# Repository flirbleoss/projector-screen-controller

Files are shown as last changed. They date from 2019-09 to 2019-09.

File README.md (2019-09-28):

# Projector Screen Controller

Simple controller for basic motorized projector screens. An _almost_-drop-in
replacement for the Da-Lite SCB-100.

Status: _Work in progress_

# Background

Tired of the commercial screen controller letting out its magic smoke every
couple of years and not content with the $400 replacement cost, I decided to
make my own _almost_-drop-in replacement with more emphasis on electronic
protection than the commercial variant seems to have.

In my analysis of both SCB-100s that failed, it appeared a transient condition
upset the MAX232 driver such that it causes a dead-short between the 5v and 0v
rails. The charge pump capacitors of the MAX232 chip are adjacent to the
ULN2003 relay driver and the 12V decoupling capacitor. The design relies on
the diodes in the ULN2003 for back-EMF suppression, which I speculate may not
be adequate for the off-brand relays in use in both of my SCB-100s (an online
search reveals other specimens have relays from a more reputable brand,
however.) Finally, the switching power supply module is soldered to the back
of the logic board. While there is a plastic divider between the boards, there
is only a few milimeters of space and line voltage spikes may well cause
interference; additionally there are several places where line voltage and
signal voltage traces come closer than I would be comfortable with.

It is my conclusion therefore that the failures are likely caused by
insufficient physical isolation and insufficient transient back-EMF
suppression.

## Design objectives

* Same form-factor for the board, so it can use the same metal case
  in-situ.
* Connections in roughly the same locations, with the same pin ordering.
* Use removable Phoenix connectors with screw terminals throughout.
* Improved electronic protection;
  * Better flyback suppression from the relays.
  * DC power protection in case the power supply fails.
  * Physical board isolation (with board cut-outs) between line voltages
    and the 5V/12V sections, especially around the relays.
  * Better isolation between 12V and 5V sections, to avoid relay noise
    issues.
  * Modern high-efficiency switching power supply with plenty of
    protection features.
* More indicator LEDs to show what is going on.
* Backward-compatible RS232 protocol, but enhancements to allow
  customizing, for example, the motor run time.
* Open-source design.

# Implementation

## Preview

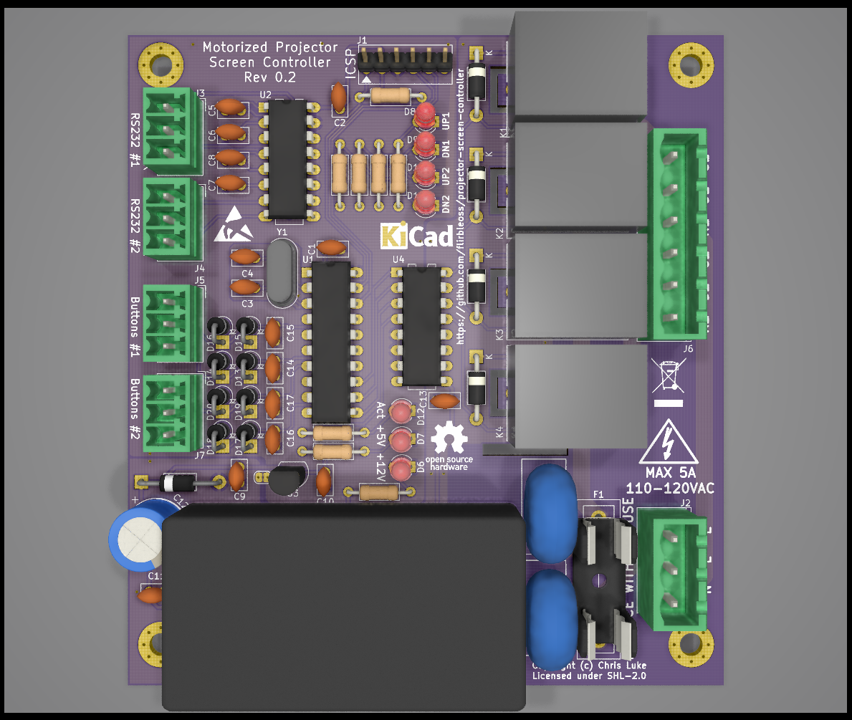
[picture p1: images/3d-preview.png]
3D board preview (with components)

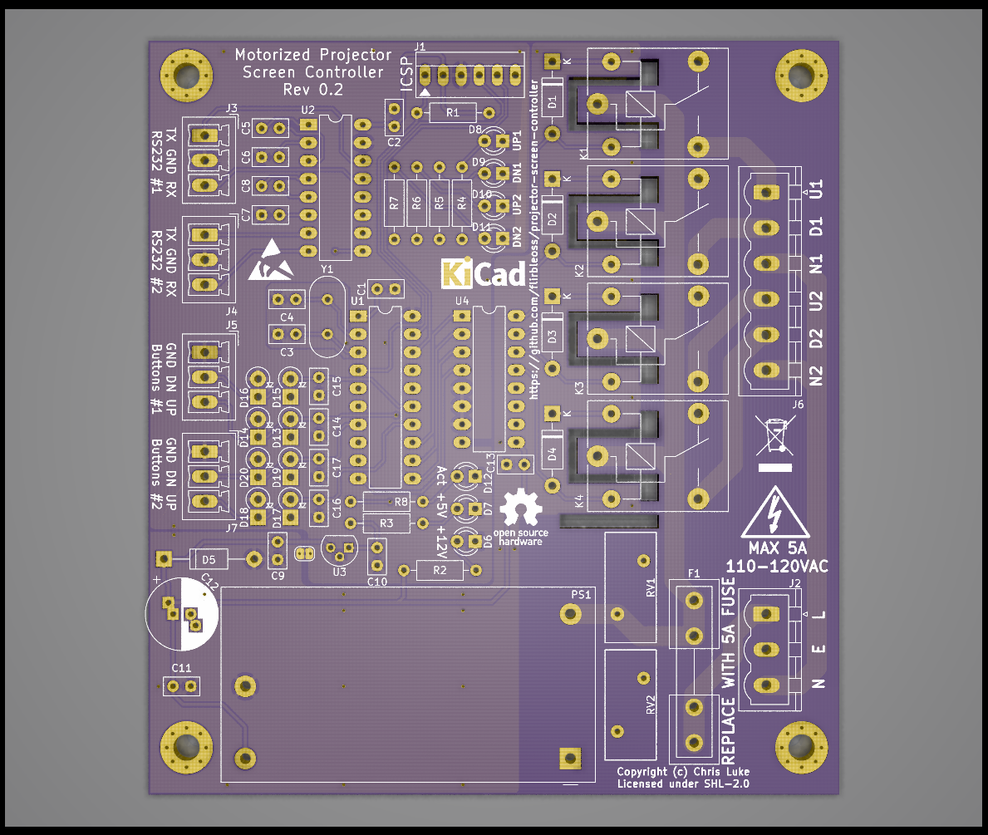
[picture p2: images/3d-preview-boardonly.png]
3D board preview (board only)


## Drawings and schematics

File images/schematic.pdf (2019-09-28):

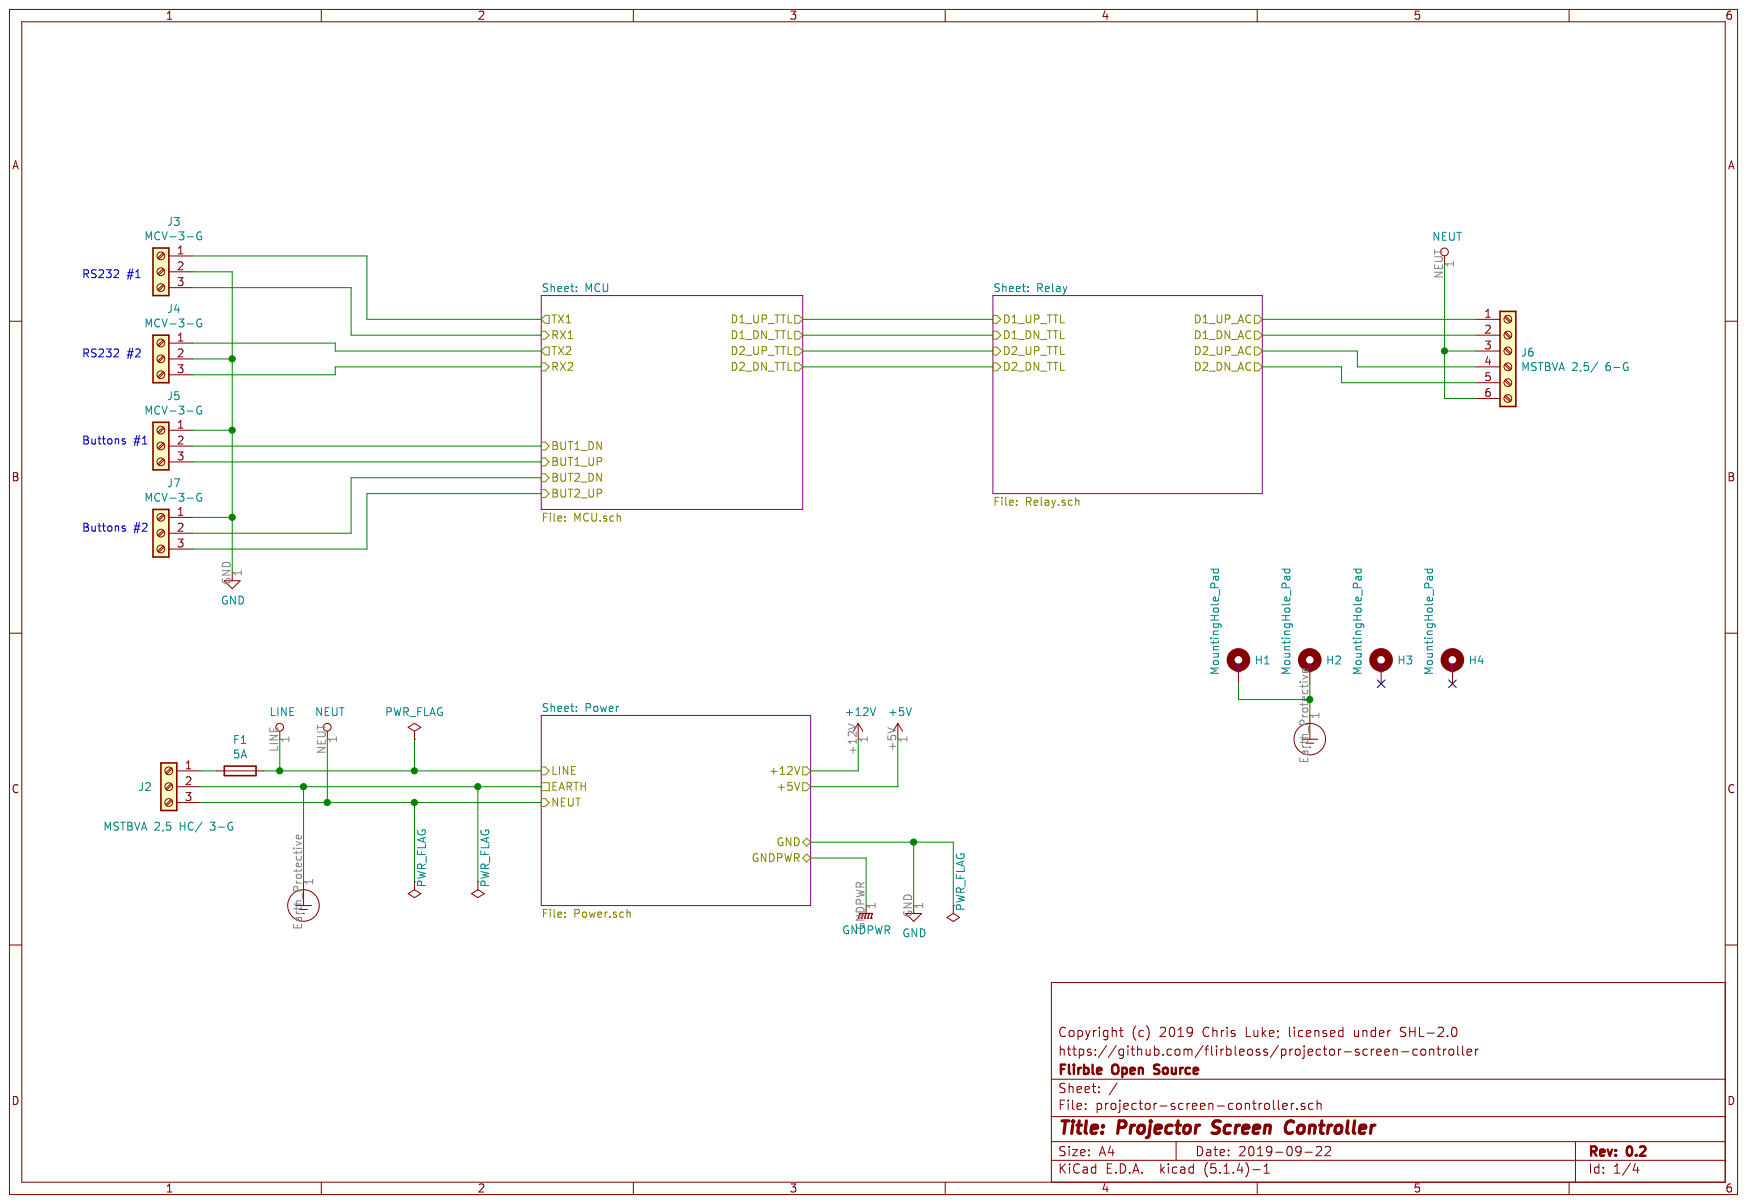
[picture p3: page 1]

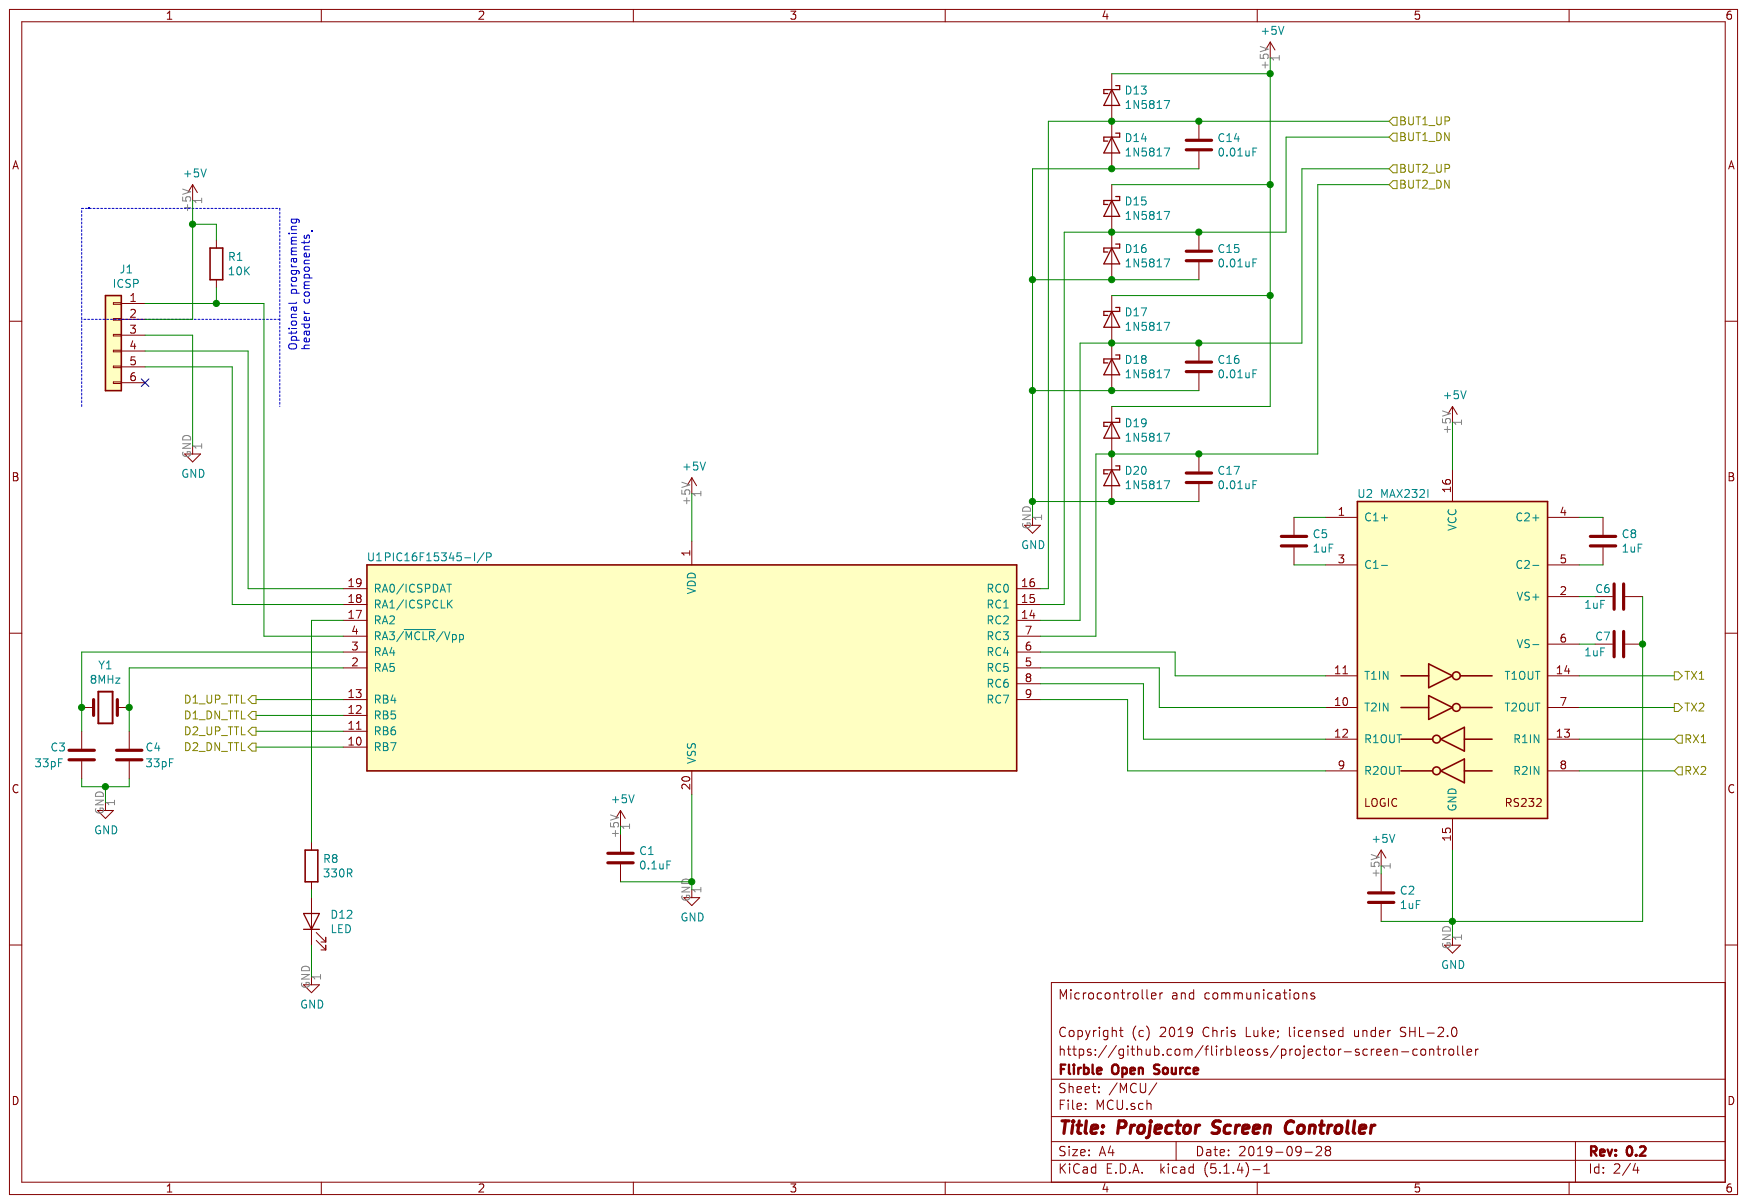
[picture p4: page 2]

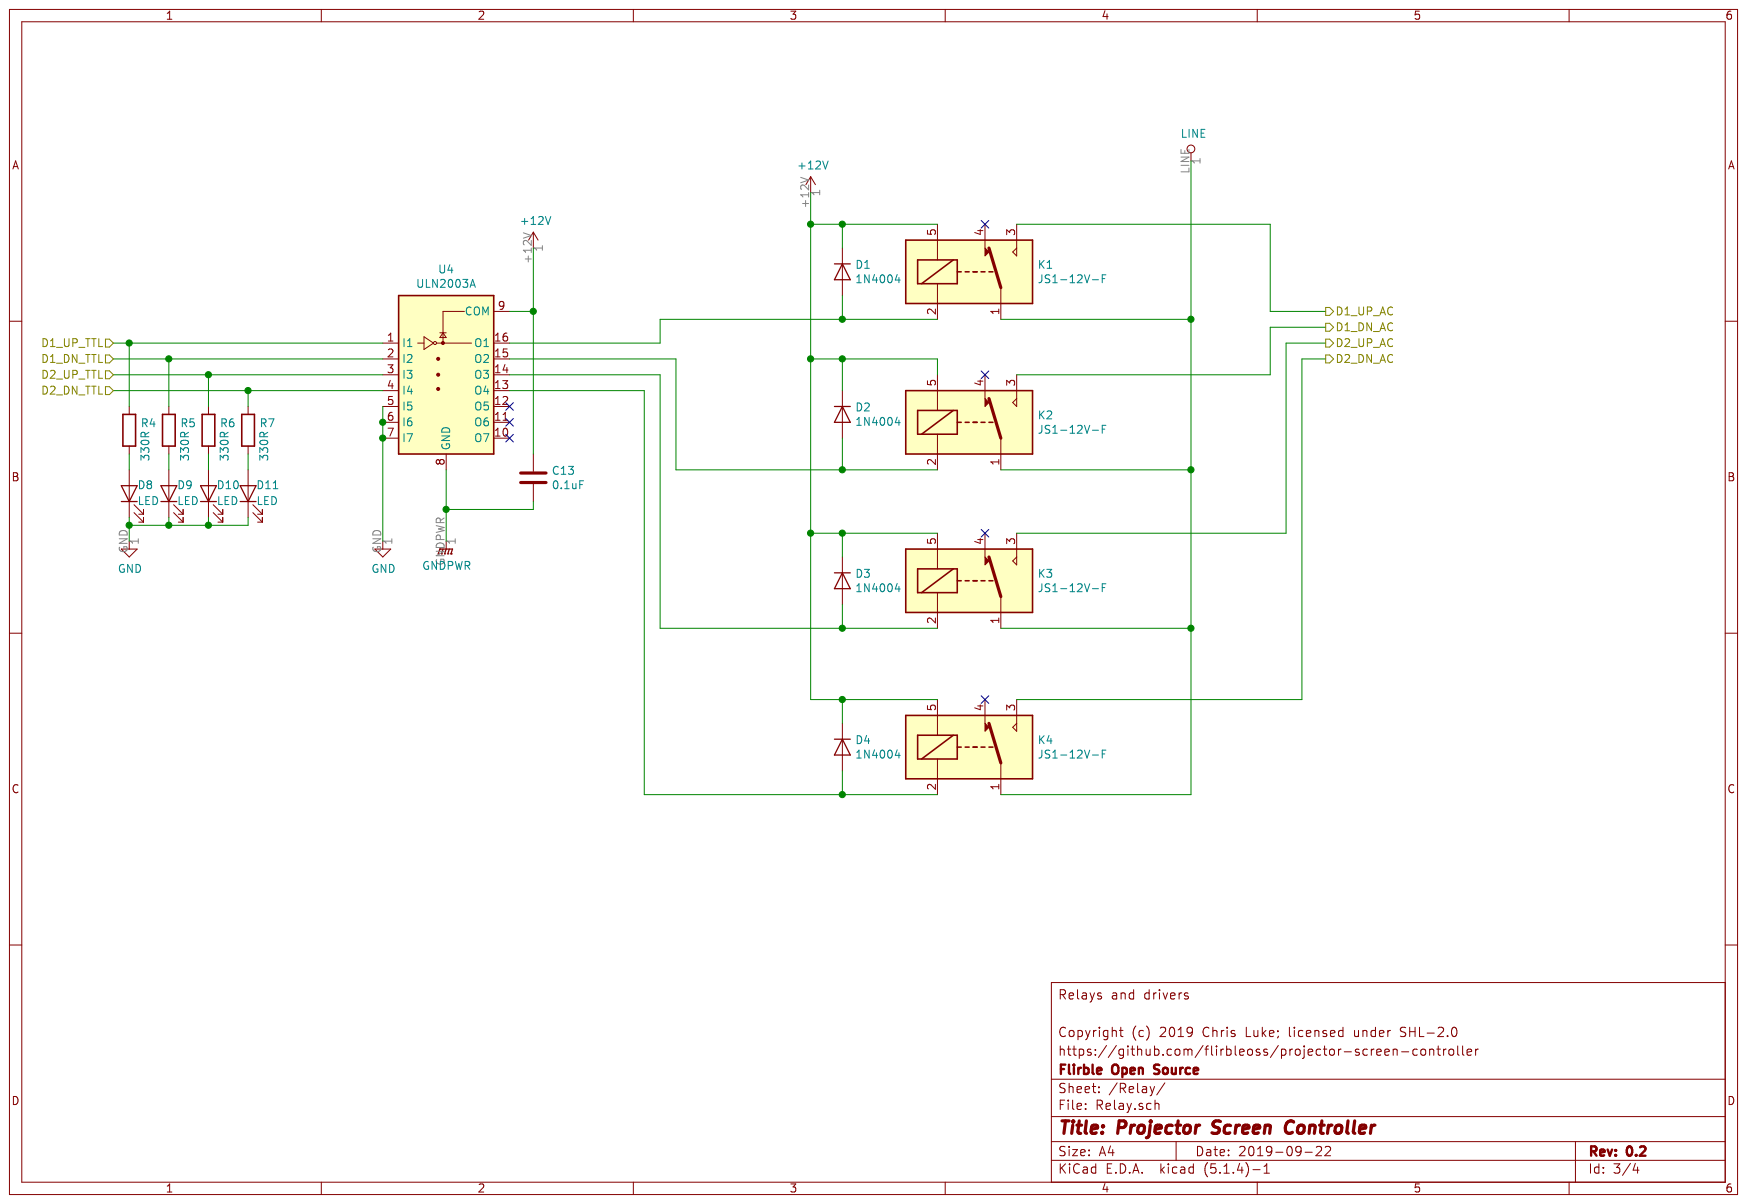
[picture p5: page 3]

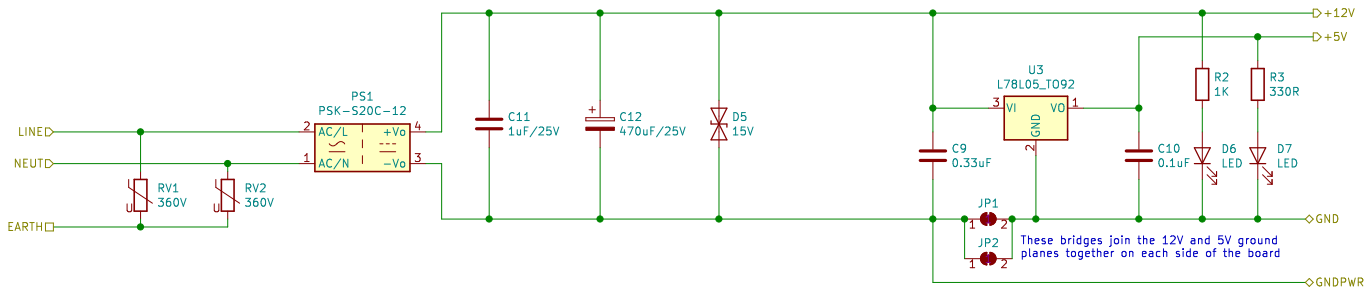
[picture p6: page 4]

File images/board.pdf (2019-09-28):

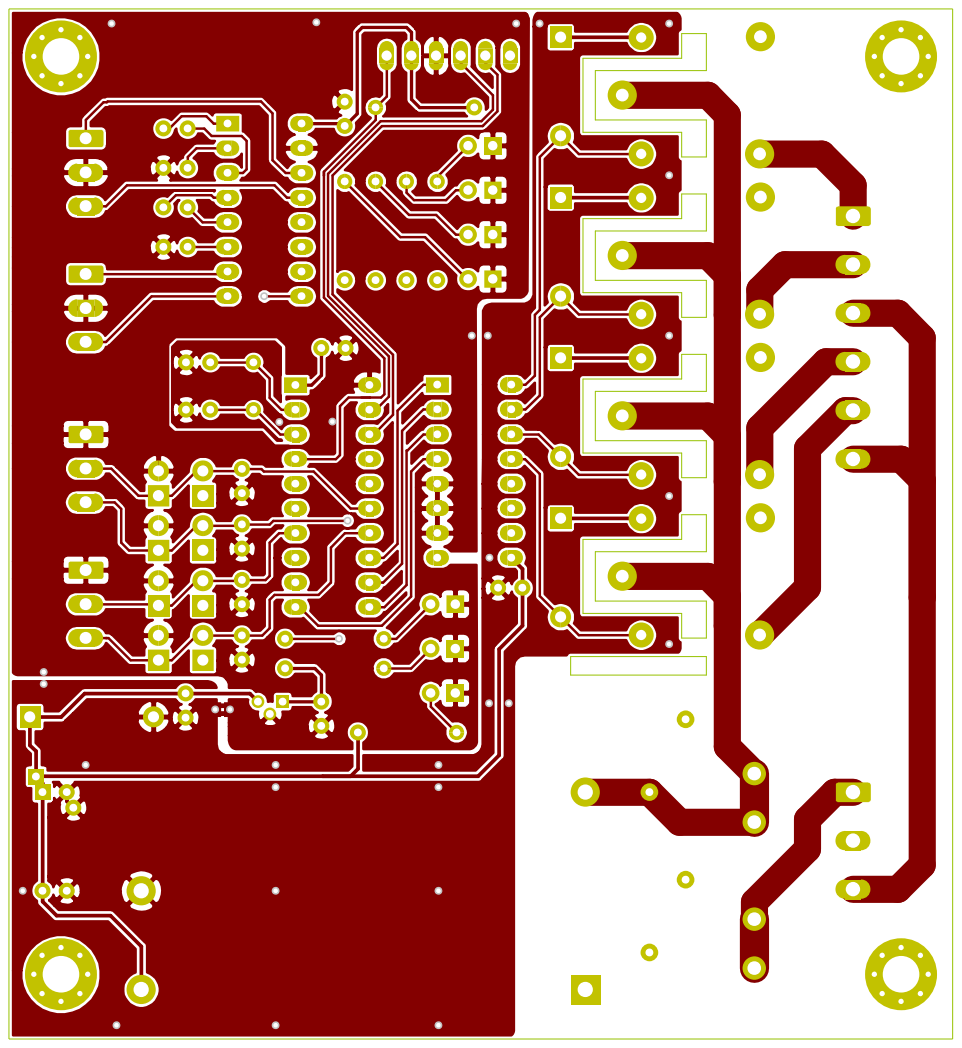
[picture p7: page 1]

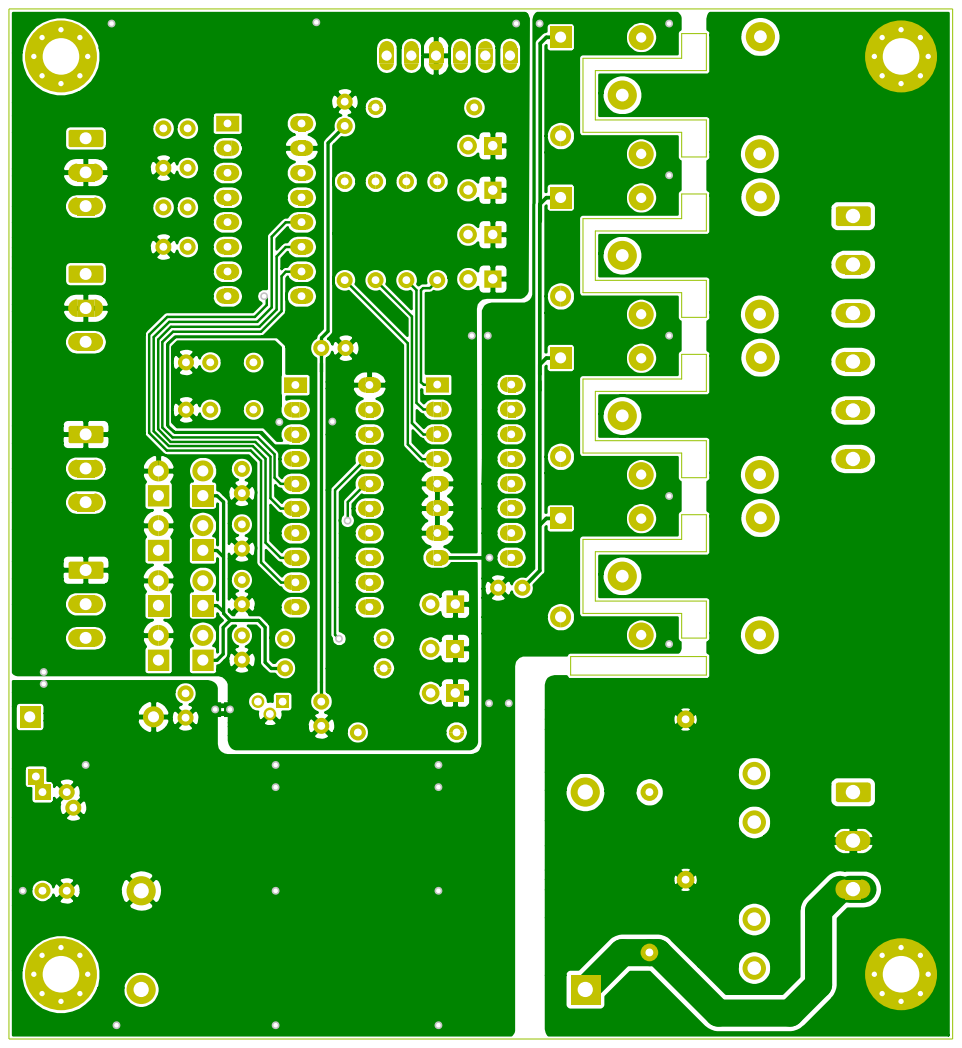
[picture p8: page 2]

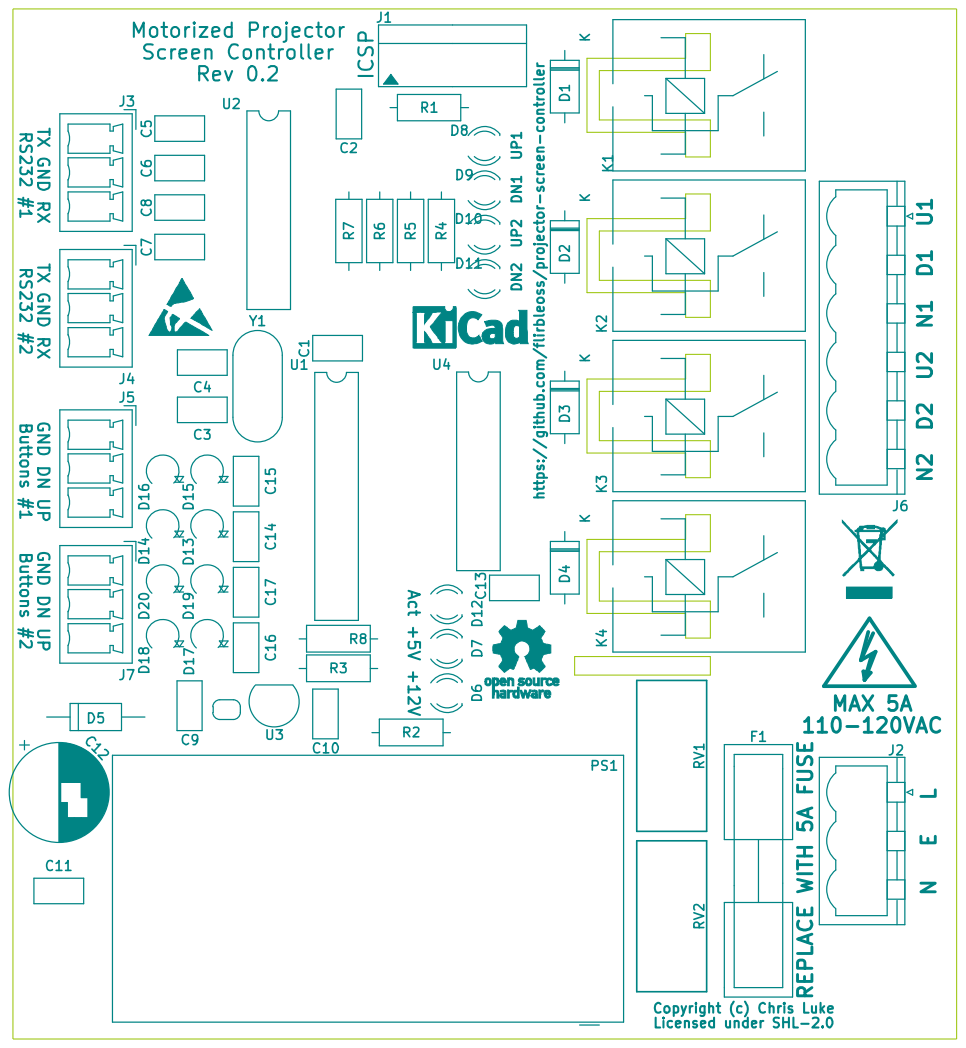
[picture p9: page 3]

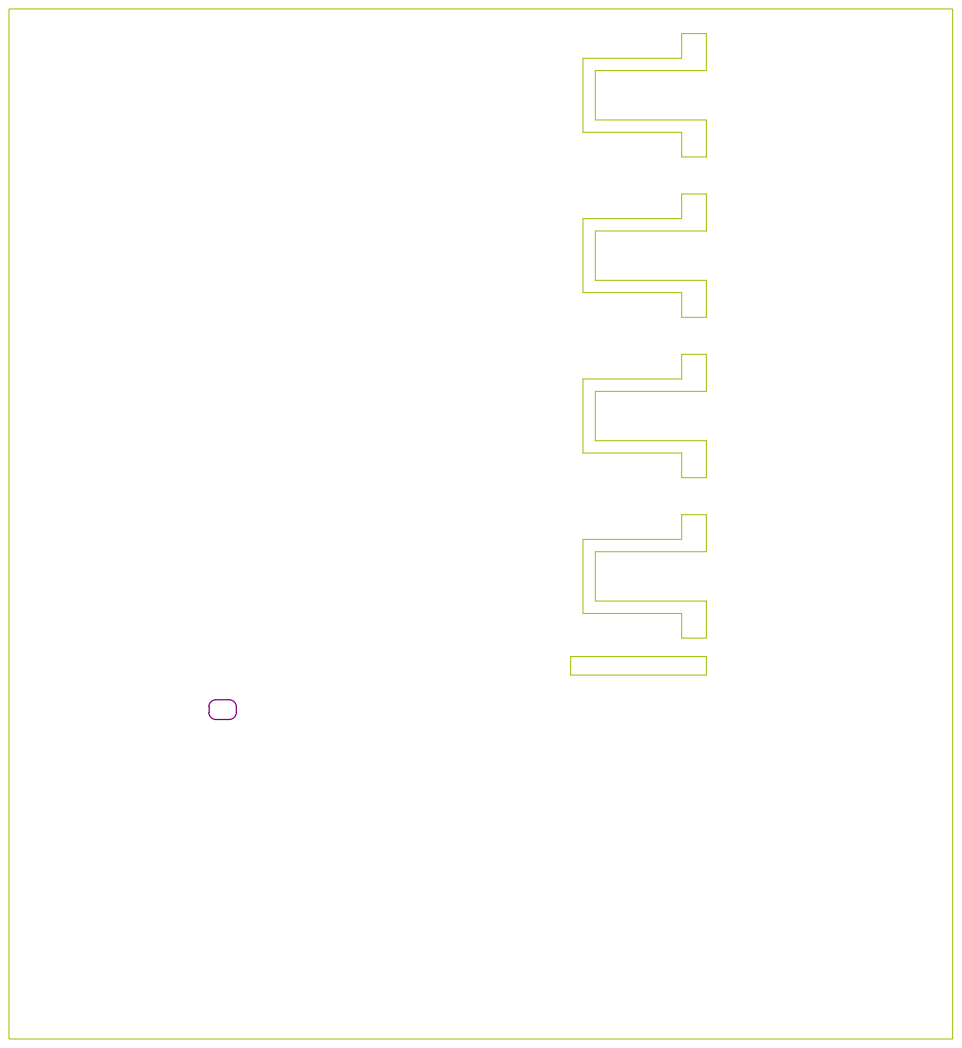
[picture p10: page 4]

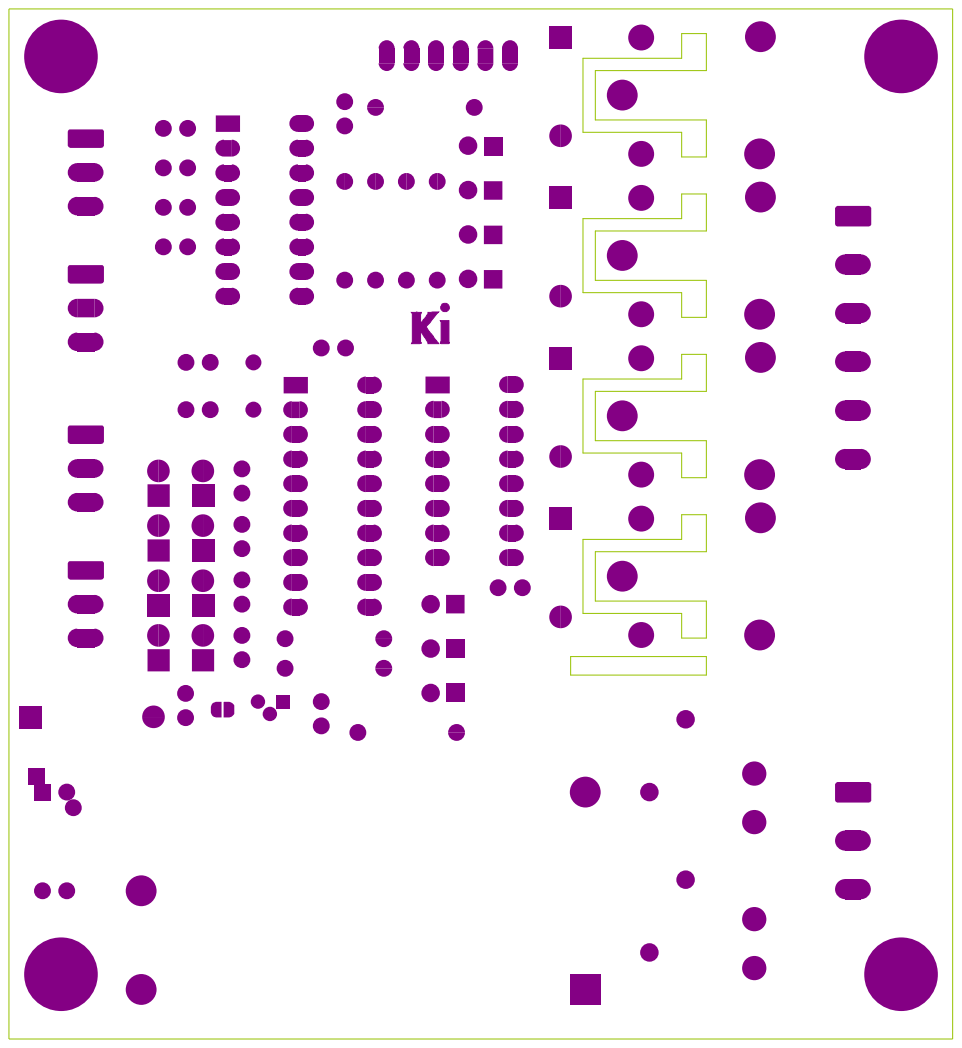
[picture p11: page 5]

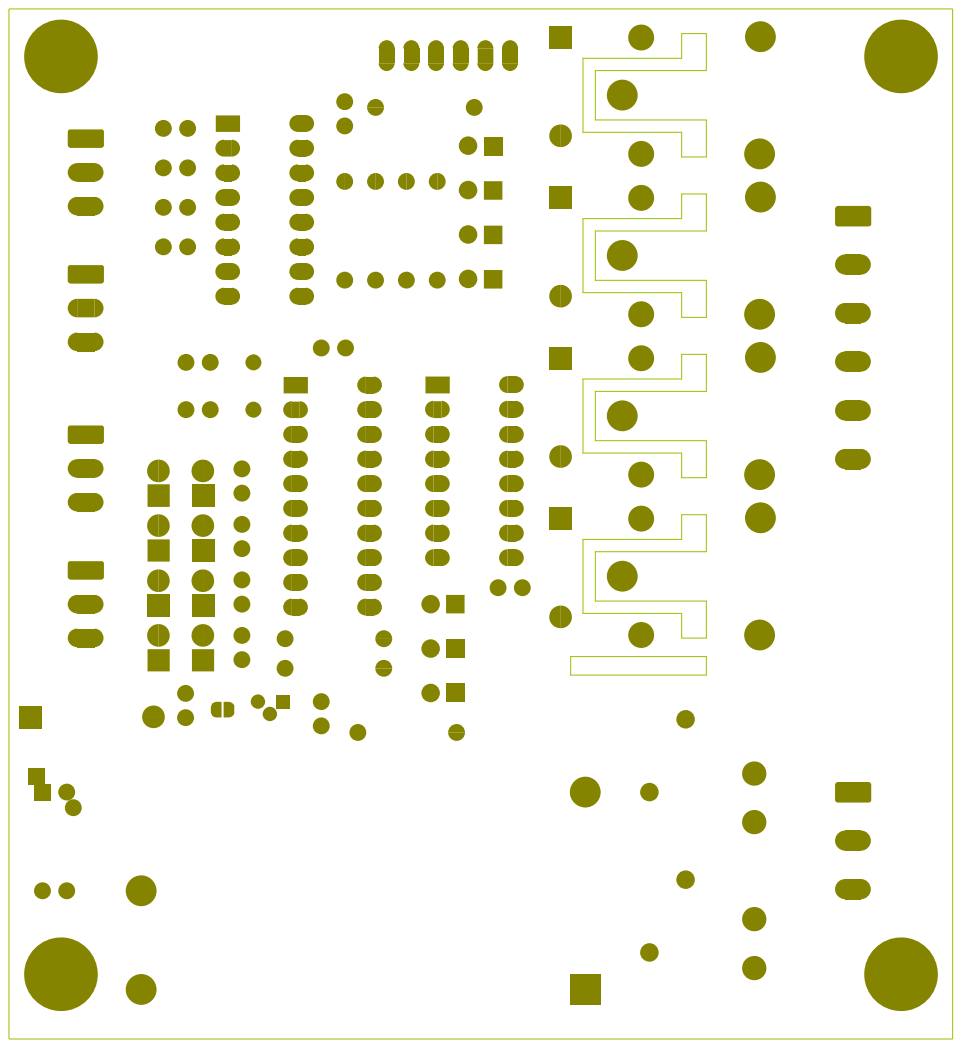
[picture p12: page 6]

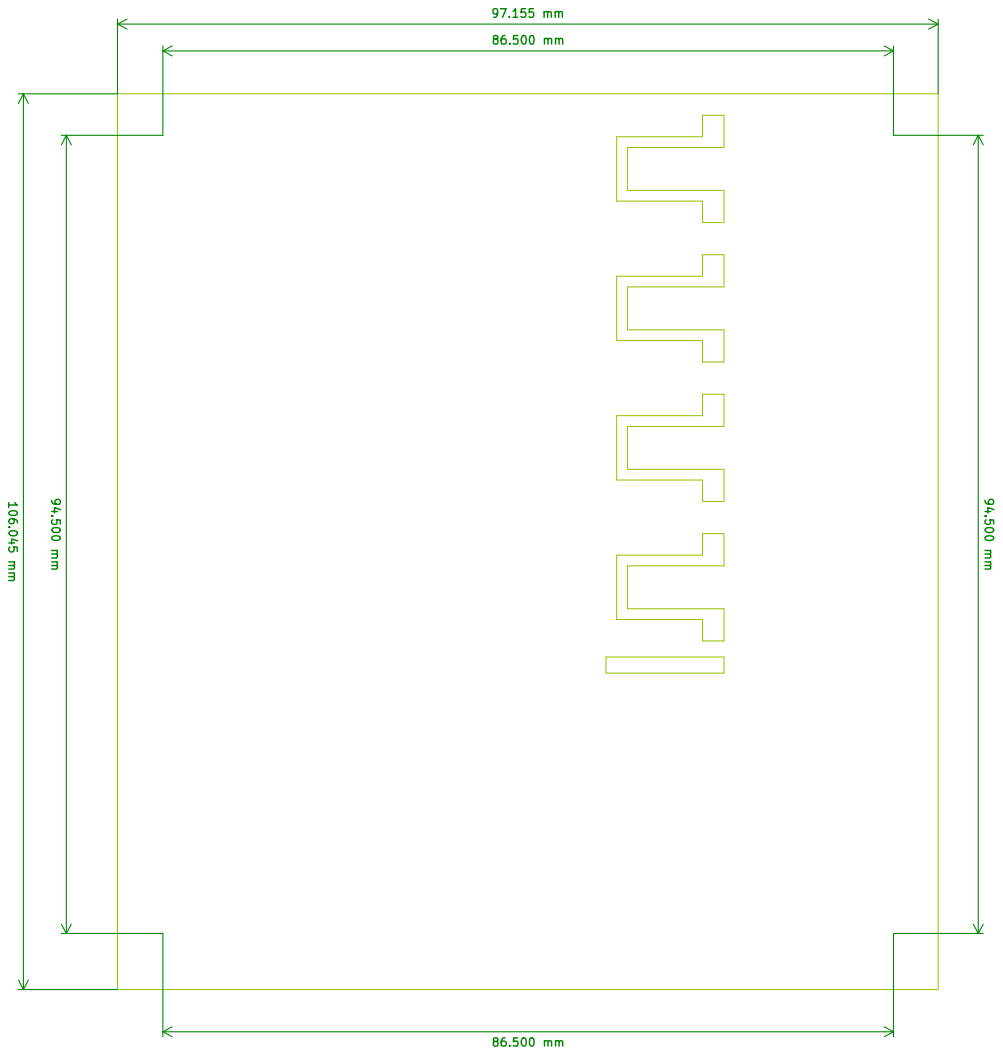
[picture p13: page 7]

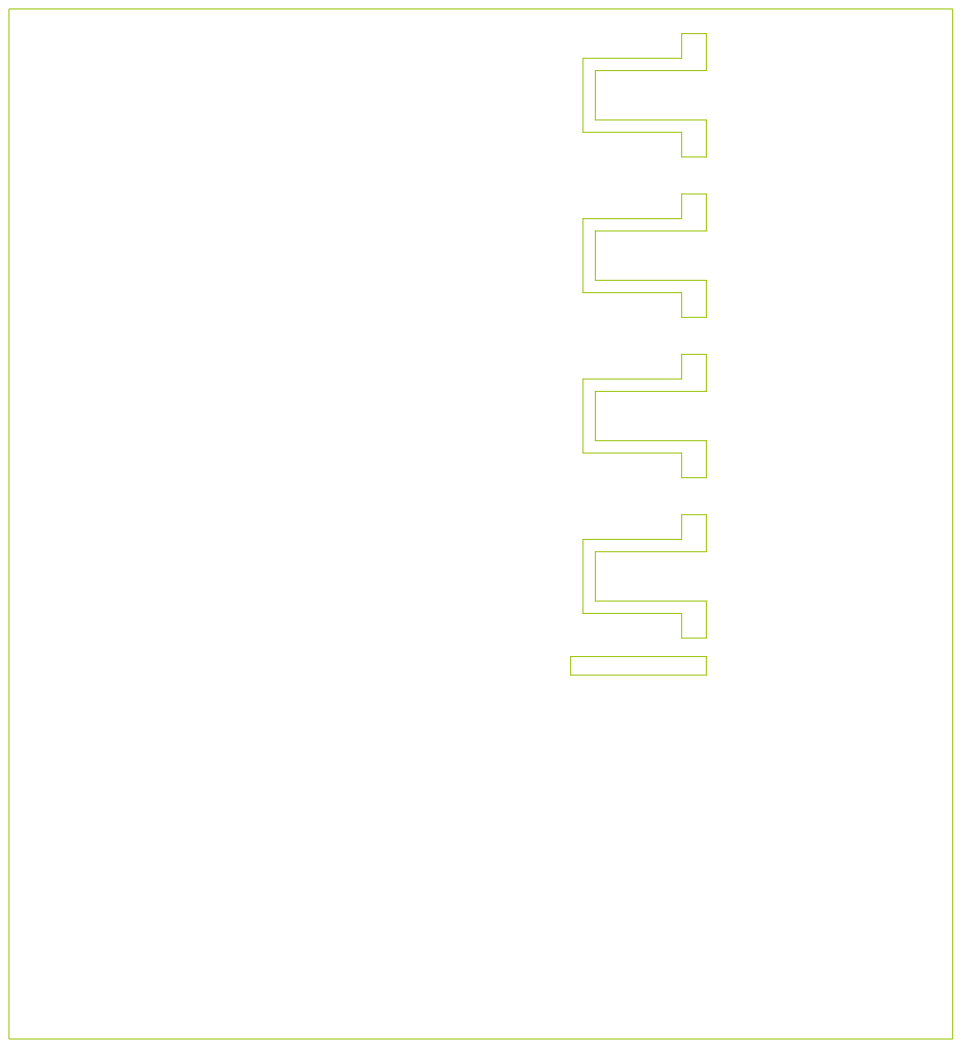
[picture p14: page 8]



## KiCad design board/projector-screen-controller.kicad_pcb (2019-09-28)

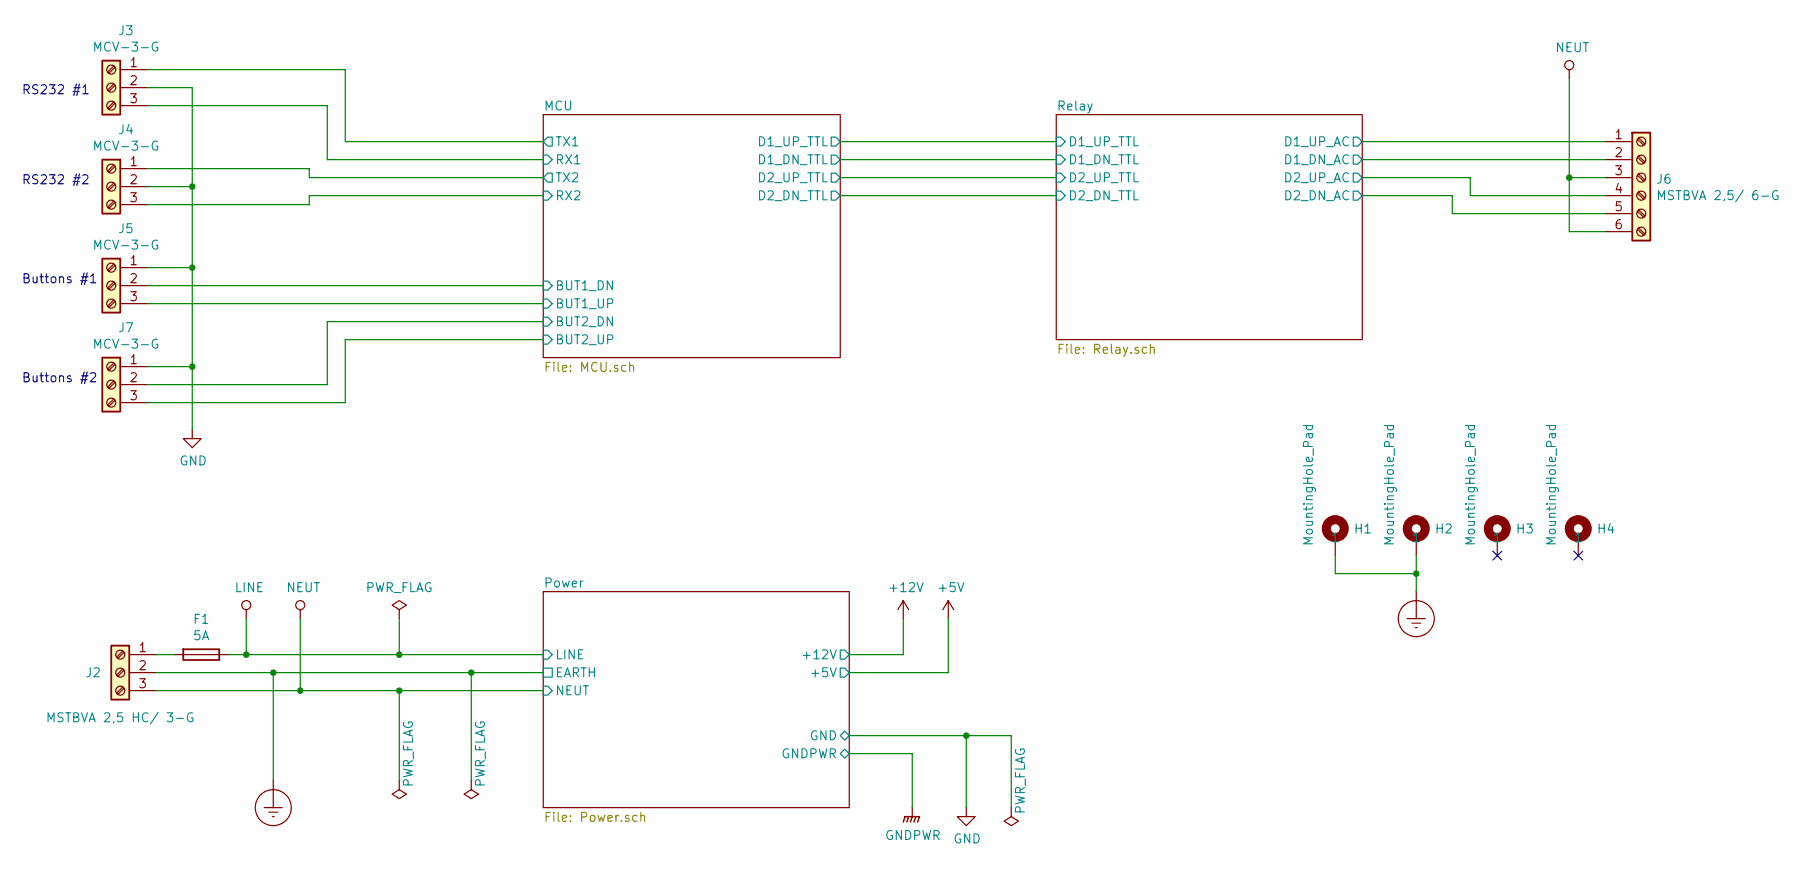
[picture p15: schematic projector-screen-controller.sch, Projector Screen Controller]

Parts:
F1: 5A; Fuseholder5x20_horiz_open_inline_Type-I
H1, H2, H3, H4: MountingHole_Pad; MountingHole_3.7mm_Pad_Via
J2: MSTBVA 2,5 HC/ 3-G; PhoenixContact_MSTBVA_2,5_3-G_1x03_P5.00mm_Vertical; mpn 1924208
J3, J4, J5, J7: MCV-3-G; PhoenixContact_MCV_1,5_3-G-3.5_1x03_P3.50mm_Vertical; mpn 1843619
J6: MSTBVA 2,5/ 6-G; PhoenixContact_MSTBVA_2,5_6-G_1x06_P5.00mm_Vertical; mpn 1755558

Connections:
/MCU/BUT1_DN: J5.2; also elsewhere on the board
/MCU/BUT1_UP: J5.3; also elsewhere on the board
/MCU/BUT2_DN: J7.2; also elsewhere on the board
/MCU/BUT2_UP: J7.3; also elsewhere on the board
/MCU/RX1: J3.3; also elsewhere on the board
/MCU/RX2: J4.3; also elsewhere on the board
/MCU/TX1: J3.1; also elsewhere on the board
/MCU/TX2: J4.1; also elsewhere on the board
/Relay/D1_DN_AC: J6.2; also elsewhere on the board
/Relay/D1_UP_AC: J6.1; also elsewhere on the board
/Relay/D2_DN_AC: J6.5; also elsewhere on the board
/Relay/D2_UP_AC: J6.4; also elsewhere on the board
Earth_Protective: H1.1, H2.1, J2.2; also elsewhere on the board
GND: J3.2, J4.2, J5.1, J7.1; also elsewhere on the board
LINE: F1.1; also elsewhere on the board
NEUT: J2.3, J6.3, J6.6; also elsewhere on the board
unnamed: F1.2, J2.1

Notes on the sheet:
RS232 #1
RS232 #2
Buttons #1
Buttons #2

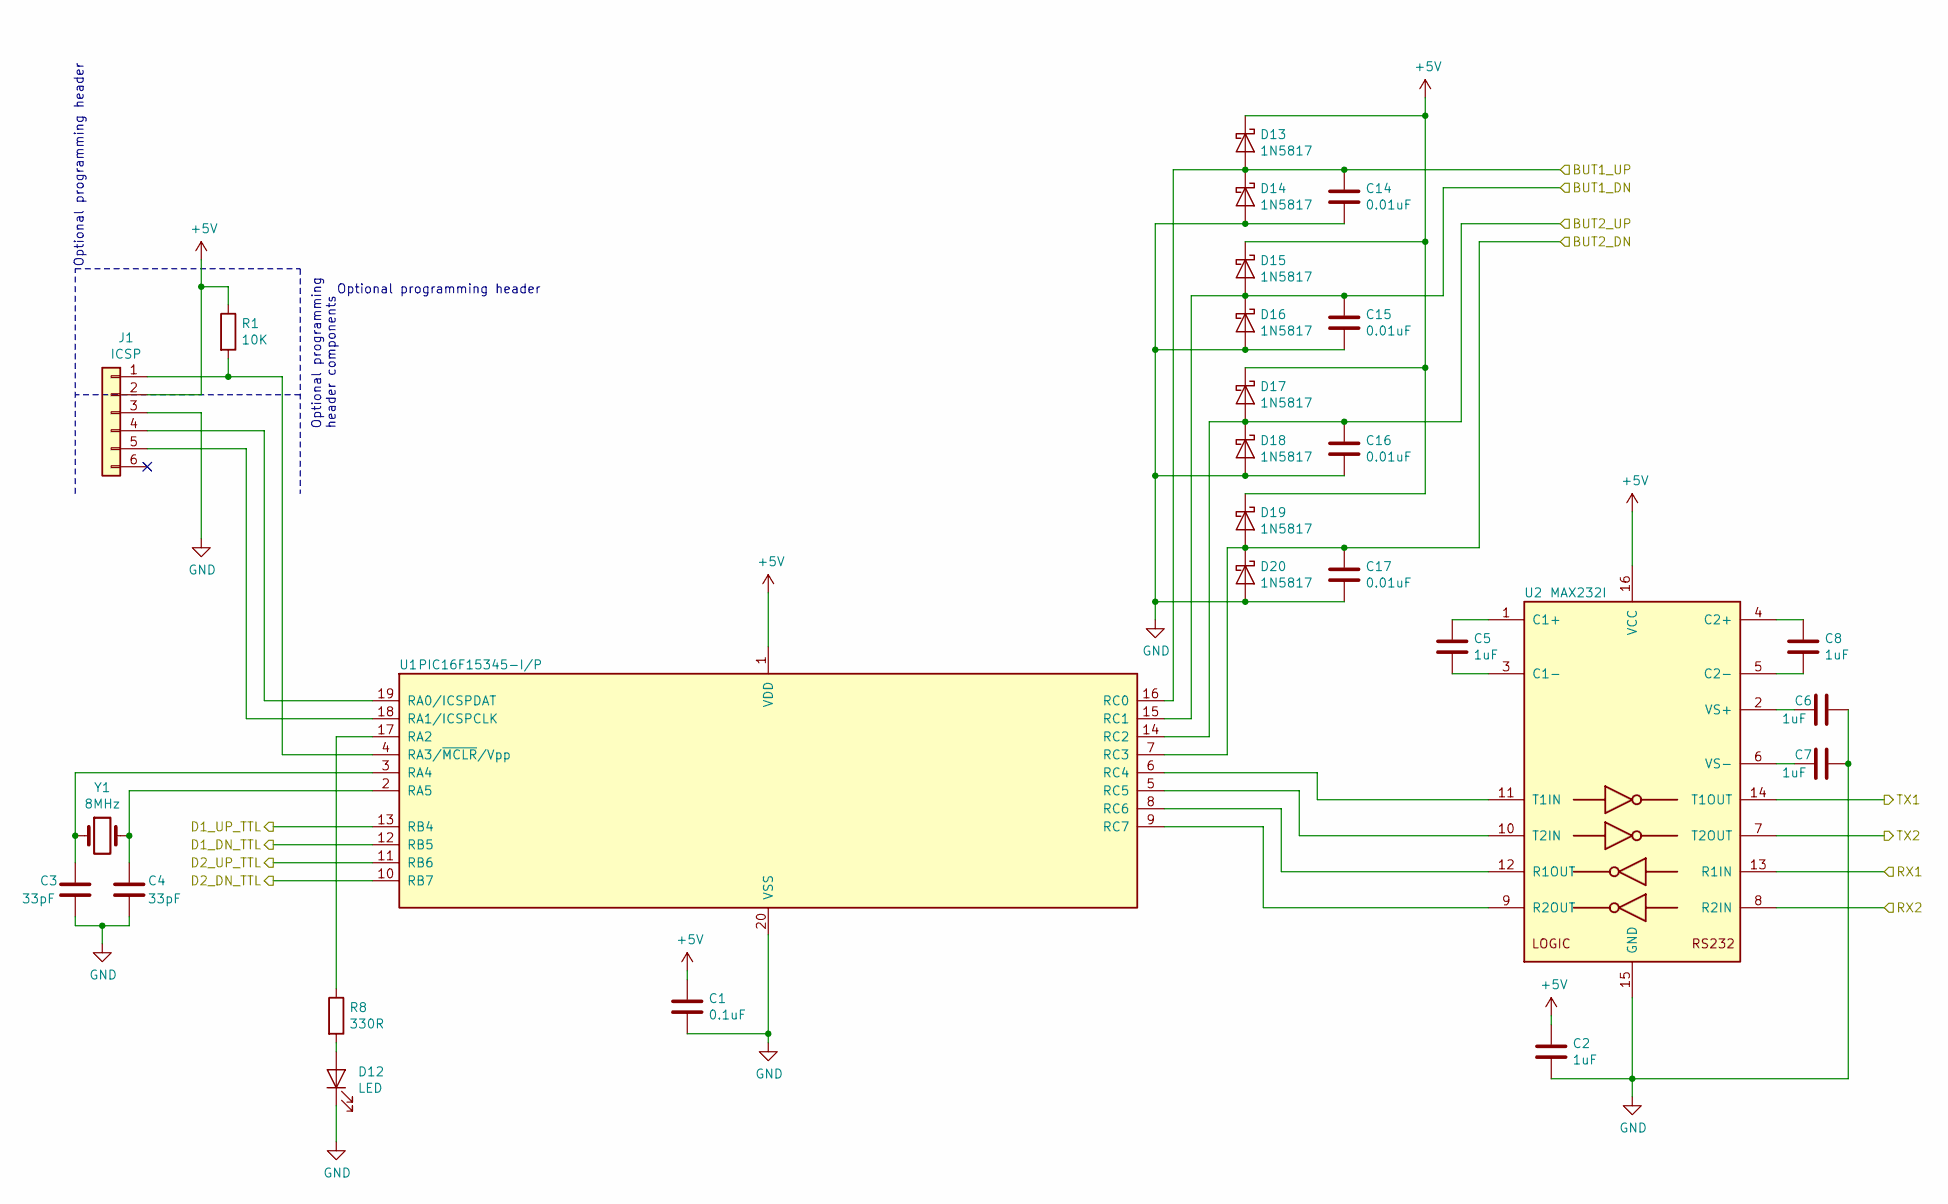
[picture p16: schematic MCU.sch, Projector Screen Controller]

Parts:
C1: 0.1uF; C_Disc_D5.0mm_W2.5mm_P2.50mm
C2, C5, C6, C7, C8: 1uF; C_Disc_D5.0mm_W2.5mm_P2.50mm
C3, C4: 33pF; C_Disc_D5.0mm_W2.5mm_P2.50mm; mpn FG18C0G1H330JNT06
C14, C15, C16, C17: 0.01uF; C_Disc_D5.0mm_W2.5mm_P2.50mm
D12: LED; LED_D3.0mm
D13, D14, D15, D16, D17, D18, D19, D20: 1N5817; D_DO-41_SOD81_P2.54mm_Vertical_KathodeUp
J1: ICSP; PINHEAD1-6
R1: 10K; R_Axial_DIN0207_L6.3mm_D2.5mm_P10.16mm_Horizontal
R8: 330R; R_Axial_DIN0207_L6.3mm_D2.5mm_P10.16mm_Horizontal
U1: PIC16F15345-I/P; DIP-20_W7.62mm_LongPads; mpn PIC16F15345-I/P
U2: MAX232I; DIP-16_W7.62mm_LongPads; mpn MAX232IN
Y1: 8MHz; Crystal_HC49-4H_Vertical; mpn XT9S20ANA8M

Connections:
+5V: C1.1, C2.1, D13.1 (K), D15.1 (K), D17.1 (K), D19.1 (K), J1.2, R1.1, U1.1 (VDD), U2.16 (VCC); also elsewhere on the board
/MCU/BUT1_DN: C15.1, D15.2 (A), D16.1 (K), U1.15 (RC1); also elsewhere on the board
/MCU/BUT1_UP: C14.1, D13.2 (A), D14.1 (K), U1.16 (RC0); also elsewhere on the board
/MCU/BUT2_DN: C17.1, D19.2 (A), D20.1 (K), U1.7 (RC3); also elsewhere on the board
/MCU/BUT2_UP: C16.1, D17.2 (A), D18.1 (K), U1.14 (RC2); also elsewhere on the board
/MCU/D1_DN_TTL: U1.12 (RB5); also elsewhere on the board
/MCU/D1_UP_TTL: U1.13 (RB4); also elsewhere on the board
/MCU/D2_DN_TTL: U1.10 (RB7); also elsewhere on the board
/MCU/D2_UP_TTL: U1.11 (RB6); also elsewhere on the board
/MCU/RX1: U2.13 (R1IN); also elsewhere on the board
/MCU/RX2: U2.8 (R2IN); also elsewhere on the board
/MCU/TX1: U2.14 (T1OUT); also elsewhere on the board
/MCU/TX2: U2.7 (T2OUT); also elsewhere on the board
GND: C1.2, C2.2, C3.2, C4.2, C6.1, C7.1, C14.2, C15.2, C16.2, C17.2, D12.1 (K), D14.2 (A), D16.2 (A), D18.2 (A), D20.2 (A), J1.3, U1.20 (VSS), U2.15 (GND); also elsewhere on the board
unnamed: C3.1, U1.3 (RA4), Y1.1
unnamed: C4.1, U1.2 (RA5), Y1.2
unnamed: C5.1, U2.1 (C1+)
unnamed: C5.2, U2.3 (C1-)
unnamed: C6.2, U2.2 (VS+)
unnamed: C7.2, U2.6 (VS-)
unnamed: C8.1, U2.4 (C2+)
unnamed: C8.2, U2.5 (C2-)
unnamed: D12.2 (A), R8.2
unnamed: J1.1, R1.2, U1.4 (RA3/~MCLR~/Vpp)
unnamed: J1.4, U1.19 (RA0/ICSPDAT)
unnamed: J1.5, U1.18 (RA1/ICSPCLK)
unnamed: R8.1, U1.17 (RA2)
unnamed: U1.5 (RC5), U2.10 (T2IN)
unnamed: U1.6 (RC4), U2.11 (T1IN)
unnamed: U1.8 (RC6), U2.12 (R1OUT)
unnamed: U1.9 (RC7), U2.9 (R2OUT)

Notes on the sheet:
Optional programming header
Optional programming header components

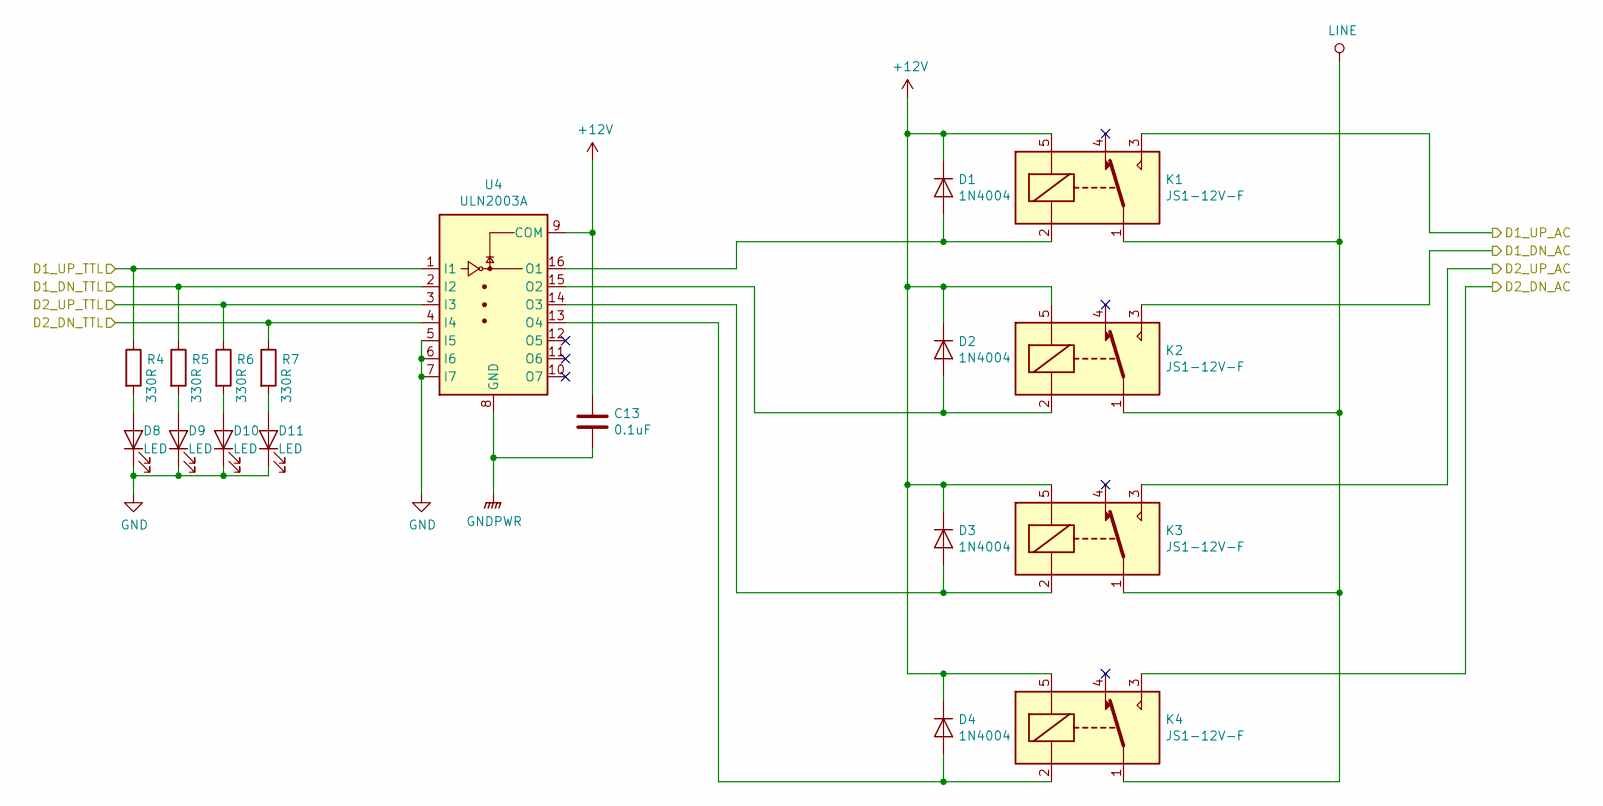
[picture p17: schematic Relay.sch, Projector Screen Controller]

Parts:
C13: 0.1uF; C_Disc_D5.0mm_W2.5mm_P2.50mm
D1, D2, D3, D4: 1N4004; D_DO-41_SOD81_P10.16mm_Horizontal
D8, D9, D10, D11: LED; LED_D3.0mm
K1, K2, K3, K4: JS1-12V-F; Relay_SPDT_SANYOU_SRD_Series_Form_C; mpn JS1-12V-F
R4, R5, R6, R7: 330R; R_Axial_DIN0207_L6.3mm_D2.5mm_P10.16mm_Horizontal
U4: ULN2003A; DIP-16_W7.62mm_LongPads; mpn ULN2003A

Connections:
+12V: C13.1, D1.1 (K), D2.1 (K), D3.1 (K), D4.1 (K), K1.5, K2.5, K3.5, K4.5, U4.9 (COM); also elsewhere on the board
/MCU/D1_DN_TTL: R5.1, U4.2 (I2); also elsewhere on the board
/MCU/D1_UP_TTL: R4.1, U4.1 (I1); also elsewhere on the board
/MCU/D2_DN_TTL: R7.1, U4.4 (I4); also elsewhere on the board
/MCU/D2_UP_TTL: R6.1, U4.3 (I3); also elsewhere on the board
/Relay/D1_DN_AC: K2.3; also elsewhere on the board
/Relay/D1_UP_AC: K1.3; also elsewhere on the board
/Relay/D2_DN_AC: K4.3; also elsewhere on the board
/Relay/D2_UP_AC: K3.3; also elsewhere on the board
GND: D8.1 (K), D9.1 (K), D10.1 (K), D11.1 (K), U4.5 (I5), U4.6 (I6), U4.7 (I7); also elsewhere on the board
GNDPWR: C13.2, U4.8 (GND); also elsewhere on the board
LINE: K1.1, K2.1, K3.1, K4.1; also elsewhere on the board
unnamed: D1.2 (A), K1.2, U4.16 (O1)
unnamed: D2.2 (A), K2.2, U4.15 (O2)
unnamed: D3.2 (A), K3.2, U4.14 (O3)
unnamed: D4.2 (A), K4.2, U4.13 (O4)
unnamed: D8.2 (A), R4.2
unnamed: D9.2 (A), R5.2
unnamed: D10.2 (A), R6.2
unnamed: D11.2 (A), R7.2

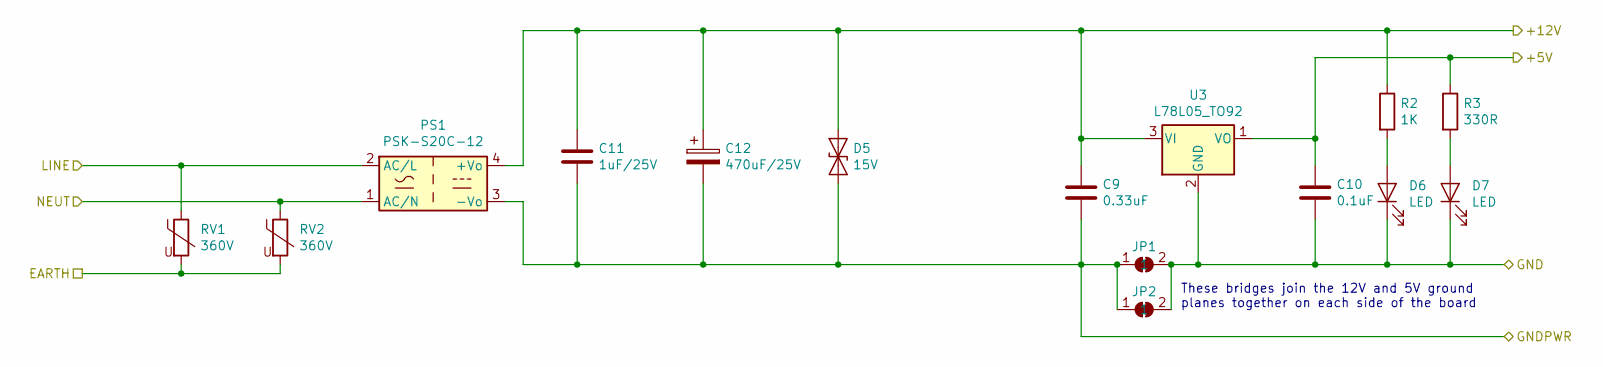
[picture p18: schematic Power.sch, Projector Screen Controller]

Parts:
C9: 0.33uF; C_Disc_D5.0mm_W2.5mm_P2.50mm; mpn FG18X7R1H334KRT00
C10: 0.1uF; C_Disc_D5.0mm_W2.5mm_P2.50mm; mpn FG18X7R1H104KNT06
C11: 1uF/25V; C_Disc_D5.0mm_W2.5mm_P2.50mm; mpn FG18X7R1E105KRT00
C12: 470uF/25V; CP_Radial_D10.0mm_P2.50mm_P5.00mm; mpn UPW1E471MPD
D5: 15V; D_DO-41_SOD81_P12.70mm_Horizontal; mpn 1.5KE15CA-E3/54
D6, D7: LED; LED_D3.0mm
JP1, JP2: SolderJumper_2_Bridged; SolderJumper-2_P1.3mm_Bridged2Bar_RoundedPad1.0x1.5mm
PS1: PSK-S20C-12; ACDC-Conv_CUI-PSK-S20C; mpn PSK-S20C-12
R2: 1K; R_Axial_DIN0207_L6.3mm_D2.5mm_P10.16mm_Horizontal
R3: 330R; R_Axial_DIN0207_L6.3mm_D2.5mm_P10.16mm_Horizontal
RV1, RV2: 360V; RV_Disc_D15.5_W7.2_P7.5; mpn VDRS14T230BSE
U3: L78L05_TO92; TO-92L; mpn L78L05ABZ-TR

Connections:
+5V: C10.1, R3.1, U3.1 (VO); also elsewhere on the board
+12V: C9.1, C11.1, C12.1, D5.1 (A1), PS1.4 (+Vo), R2.1, U3.3 (VI); also elsewhere on the board
Earth_Protective: RV1.2, RV2.2; also elsewhere on the board
GND: C10.2, D6.1 (K), D7.1 (K), JP1.2 (B), JP2.2 (B), U3.2 (GND); also elsewhere on the board
GNDPWR: C9.2, C11.2, C12.2, D5.2 (A2), JP1.1 (A), JP2.1 (A), PS1.3 (-Vo); also elsewhere on the board
LINE: PS1.2 (AC/L), RV1.1; also elsewhere on the board
NEUT: PS1.1 (AC/N), RV2.1; also elsewhere on the board
unnamed: D6.2 (A), R2.2
unnamed: D7.2 (A), R3.2

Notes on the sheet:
These bridges join the 12V and 5V ground planes together on each side of the board

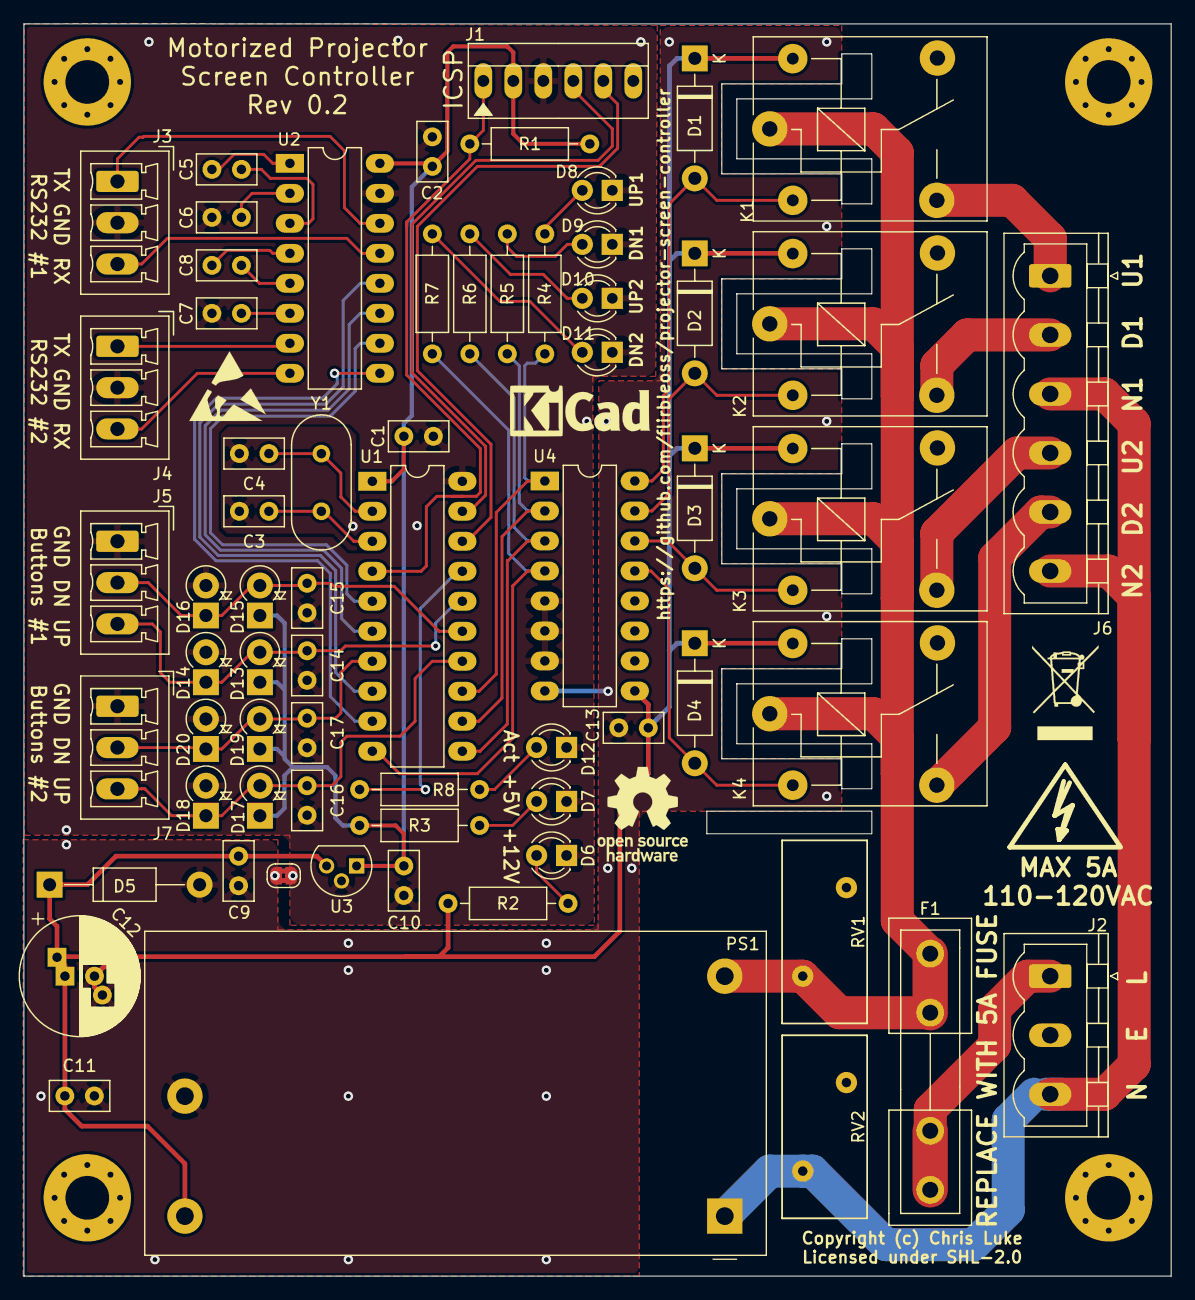
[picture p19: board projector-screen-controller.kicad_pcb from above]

Board: 2 copper layers, 97.2 x 106.0 mm, 71 parts (1 on the bottom side), 51 nets.

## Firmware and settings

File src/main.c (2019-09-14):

/*
 * Projector Screen Controller
 *
 * Copyright (c) 2019 Chris Luke. Licensed under SHL-2.0.
 * https://github.com/flirbleoss/projector-screen-controller
 */

#include "config.h"
#include <xc.h>
#include <stdint.h>
#include "pjs.h"

#ifdef USE_STDIO
#include <stdio.h>
#endif /* USE_STDIO */

#ifdef CLOCK_DEBUG
void clock_debug(void);
#endif /* CLOCK_DEBUG */

#ifdef TEST3
// Tick flag
volatile __bit ticked;
#endif

// Button de-bounce
static volatile __bit b_1upt, b_1dnt, b_2upt, b_2dnt;
static volatile __bit b_1upi, b_1dni, b_2upi, b_2dni;
static volatile __bit b_1up, b_1dn, b_2up, b_2dn;

/* Initialize the hardware peripherals.
 *
 * Clock source and speed is set by CONFIG bits in pic_config.c
 *
 * Timers:
 * TMR0: Button de-bouncing.
 * TMR1: Interval timer used to manage motor run-time.
 *
 * Pins:
 * RB4,5,6,7 are outputs that drive 4 relays, that drive motors.
 * RC0,1,2,3 are button inputs. They need weak pull-ups and interrupts.
 * RC4,5,6,7 are two sets of UART rx,tx.
 * RA0,1,3 are attached to the ICSP header.
 * RA4 may be an LED in future.
 */
static void hardware_init(void) {
    // Clock setup
    OSCENbits.EXTOEN = 1;
    OSCENbits.LFOEN = 1;

    // Disable unused modules
    PMD2 = 0xff;        // DAC, ADC, CMP, ZCD
    PMD3 = 0xff;        // PWM, CCP
    PMD5 = 0xff;        // CLC

    // Disable ADC inputs; these are enabled by default
    ANSELA = 0;
    ANSELB = 0;
    ANSELC = 0;

    // Pin re-mapping
    SSP1SSPPS = 0x00;   // Move SS1 away from RC6
    RC4PPS = 0x0f;      // RC4 -> UART 1 TX
    RC5PPS = 0x11;      // RC5 -> UART 2 TX
    RX1DTPPS = 0x16;    // RC6 -> UART 1 RX
    RX2DTPPS = 0x17;    // RC7 -> UART 2 RX
    TX1CKPPS = 0x14;    // Not used, but aligns with UART 1 RX
    TX2CKPPS = 0x15;    // Not used, but aligns with UART 2 RX

    // Disable any further more port re-mapping
    PPSLOCK = 0x55;     // Unlock the register
    PPSLOCK = 0xaa;     // Unlock the register
    PPSLOCKbits.PPSLOCKED = 1;  // Lock port maps

    // I/O setup
    LATB = 0x00;        // Make sure all outputs low (relays are off at start)
    WPUC = 0x0f;        // RC0,1,2,3 have weak pull-ups
    TRISA = 0xfb;       // RA2 is output
    TRISB = 0x00;       // Port B is all outputs
    TRISC = 0xcf;       // Port C is all inputs except UART TX pins

    // Setup interrupt-on-change for RC0,1,2,3
    IOCCN = 0x0f;       // IOC on falling edge of RC0,1,2,3
    IOCCP = 0x00;
    IOCCF = 0;
    IOCIE = 1;          // IOC on

    // Setup UART1
    SP1BRG = UART_SPBRG;
    TX1STAbits.BRGH = UART_BRGH;
    BAUD1CONbits.BRG16 = UART_BRG16;
    TX1STAbits.TXEN = 1;    // Enable transmitter
    TX1STAbits.SYNC = 0;    // Asynchronous
    RC1STAbits.CREN = 1;    // Enable receiver
    RC1STAbits.SPEN = 1;    // Enable UART
    RC1IE = 1;              // Interrupt on receive

    // Setup UART2
    SP2BRG = UART_SPBRG;
    TX2STAbits.BRGH = UART_BRGH;
    BAUD2CONbits.BRG16 = UART_BRG16;
    TX2STAbits.TXEN = 1;    // Enable transmitter
    TX2STAbits.SYNC = 0;    // Asynchronous
    RC2STAbits.CREN = 1;    // Enable receiver
    RC2STAbits.SPEN = 1;    // Enable UART
    RC2IE = 1;              // Interrupt on receive

    // Setup Timer1 for our tick
    T1CLKbits.CS = SET_TMR1_CS;
    T1CONbits.CKPS = SET_TMR1_PS;
    T1CONbits.nT1SYNC = SET_TMR1_SYNC;
    T1GCONbits.GE = 0;  // No gate
    RESET_TMR1();       // Load the counter, reset the seen flag
    ENABLE_TMR1();      // Turn it on with interrupts

    // Setup Timer0 for button reading and de-bouncing
    T0CON0bits.T016BIT = 1; // 16-bit counter mode
    T0CON1bits.T0CS = SET_TMR0_CS;
    T0CON1bits.T0CKPS = SET_TMR0_PS;
    T0CON1bits.T0ASYNC = 1; // Don't synchronize with fOSC/4
    RESET_TMR0();       // Load the counter
    PAUSE_TMR0();       // Reset the flags (not seen, no interrupts)
    ENABLE_TMR0();      // Turn it on (do not touch flags)

    // Let the interrupts loose
    PEIE = 1;
    GIE = 1;
}


// Fire it all up. This function is called when the processor starts up.
// It has to program any required peripherals and then run the program loop.

void main(void) {
    // Initialize the peripherals
    hardware_init();
    uart_init();
    relay_init();
    control_init();

    uart_send(UART_1, (unsigned char *) "#PJSC " VERSION " UART1\r\n");
    uart_send(UART_2, (unsigned char *) "#PJSC " VERSION " UART2\r\n");
#ifdef CLOCK_DEBUG
    // Work out and print the current clock situation
    clock_debug();
#endif /* CLOCK_DEBUG */
#ifdef __DEBUG
    uart_send(UART_1, (unsigned char *) "#DEBUG\r\n");
    uart_send(UART_2, (unsigned char *) "#DEBUG\r\n");
#endif

#ifdef TEST3
    unsigned char t3 = 0;
#endif

    while (1) {
        // Iterate on controller operations
        command_check();
        relay_check();

        // Latch a copy of channel 1 buttons; this keeps us interrupt friendly
        char up, dn;
        di();
        up = b_1up; b_1up = 0;
        dn = b_1dn; b_1dn = 0;
        ei();

        // Check channel 1 buttons
        button_check_channel(RELAY_CH1, up, dn);

        // Latch a copy of channel 2 buttons; this keeps us interrupt friendly
        di();
        up = b_2up; b_2up = 0;
        dn = b_2dn; b_2dn = 0;
        ei();

        // Check channel 2 buttons
        button_check_channel(RELAY_CH2, up, dn);

#ifdef USE_WATCHDOG
        // Let the puppy know we're alive
        CLRWDT();
#endif /* USE_WATCHDOG */

#ifdef TEST1
        // Test 1: Alternating pattern on the LEDs/Relays
        LATB = 0xaa;
        __delay_ms(100);
        LATB = 0x55;
        __delay_ms(100);
#endif /* TEST1 */

#ifdef TEST2
        // Test 2: Echo back characters received on UART1
        while (!uart_recvempty(UART_1)) {
            unsigned char ch = uart_recvch(UART_1, UART_NONBLOCK);
            uart_sendch(UART_1, ch);
        }
        while (!uart_recvempty(UART_2)) {
            unsigned char ch = uart_recvch(UART_2, UART_NONBLOCK);
            uart_sendch(UART_2, ch);
        }
#endif /* TEST 2 */

#ifdef TEST3
        // Test 3: Timer timing
        if (ticked) {
            t3++;
            LATB = t3 << 4;

            ticked = 0;
        }
#endif /* TEST3 */
    }
}


// Interrupt handler; invoked by the processor whenever an interrupt
// occurs, here we have to work out which peripheral triggered the
// event and act accordingly.

static void __interrupt() interrupt_handler(void) {
    // Timer1 expired? This is our tick
    if (TMR1IE && TMR1IF) {
        // Reset the timer
        RESET_TMR1();

#ifdef TEST3
        ticked = 1;
#endif

        // Relays, when enabled, run for a period of time
        relay_tick();
    }

    // Timer0 expired? This is a button de-bounce delay
    if (TMR0IE && TMR0IF) {
        // Disable the timer
        RESET_TMR0();
        PAUSE_TMR0();

        // For each input that was triggered, AND the current value of that
        // input with that at the time of trigger.
#define BT_TMR_CHECK(N, F) do { \
        if (b_ ## N ## t) { \
            b_ ## N = b_ ## N ## i; \
            b_ ## N &= ~(RC ## F); \
            b_ ## N ## t = b_ ## N ## i = 0; \
        } \
} while(0)

        BT_TMR_CHECK(1up, 0);
        BT_TMR_CHECK(1dn, 1);
#ifdef BOARD_REV_0_1
        // Board rev 0.1 has channel 2 buttons backwards
        BT_TMR_CHECK(2up, 3);
        BT_TMR_CHECK(2dn, 2);
#else
        BT_TMR_CHECK(2up, 2);
        BT_TMR_CHECK(2dn, 3);
#endif /* BOARD_REV_0_1 */
    }

    // Input line changed?
    if (IOCIE && IOCIF) {
        // Button pressed?
        if (IOCCF) {
            // Reset timer0. This is to de-bounce the press
            RESET_TMR0();
            RESUME_TMR0();

            // Record the state of any button that triggered an interrupt
            // TODO: Since we only interrupt on one edge, do we need to track
            // the value here or can we infer from the fact we saw an interrupt?
            // Avoids a race condition where bouncy inputs may trigger but read
            // 0 when we read it here.
#define BT_IOC_READ(N, F) do { \
            if (IOCCFbits.IOCCF ## F) { \
                b_ ## N ## t = 1; \
                b_ ## N ## i = ~(RC ## F); \
                IOCCFbits.IOCCF ## F = 0; \
            } \
} while(0)

            BT_IOC_READ(1up, 0);
            BT_IOC_READ(1dn, 1);
#ifdef BOARD_REV_0_1
            // Board rev 0.1 has channel 2 buttons backwards
            BT_IOC_READ(2up, 3);
            BT_IOC_READ(2dn, 2);
#else
            BT_IOC_READ(2up, 2);
            BT_IOC_READ(2dn, 3);
#endif /* BOARD_REV_0_1 */
        }
    }

    // UART1 receive?
    if (RC1IE && RC1IF) {
        // Reading all the buffered bytes clears the interrupt flag
        uart_int_recv(UART_1);
    }

    // UART1 can transmit?
    if (TX1IE && TX1IF) {
        // Disable further TX-ready interrupts; will re-enable later if needed
        TX1IE = 0;
        TX1IF = 0;

        uart_int_send(UART_1);
    }

    // UART2 receive?
    if (RC2IE && RC2IF) {
        // Reading all the buffered bytes clears the flag
        uart_int_recv(UART_2);
    }

    // UART2 can transmit?
    if (TX2IE && TX2IF) {
        // Disable further TX-ready interrupts; will re-enable later if needed
        TX2IE = 0;
        TX2IF = 0;

        uart_int_send(UART_2);
    }

}

#ifdef CLOCK_DEBUG

void clock_debug(void) {
    // Work out and print the current clock situation
    char *str;
    int val;

    printf("#DBG Main osccilator: %s\r\n",
            (OSCCON3bits.ORDY ? "Ready" : "Not Ready"));

    switch (OSCCON2bits.COSC) {
    case 0b111:
        str = "EXTOSC";
        break;
    case 0b110:
        str = "HFINTOSC (1MHz)";
        break;
    case 0b101:
        str = "LFINTOSC";
        break;
    case 0b100:
        str = "SOSC";
        break;
    case 0b010:
        str = "EXTOSC with 4x PLL";
        break;
    case 0b001:
        str = "HFINTOSC with 2x PLL (32 MHz)";
        break;
    case 0b011:
    case 0b000:
    default:
        str = "Reserved";
        break;
    }
    printf("#DBG Clock source: %s\r\n", str);

    if (OSCCON2bits.CDIV <= 0b1001) {
        val = (int)(1 << OSCCON2bits.CDIV);
        printf("#DBG Clock divider: 1:%d\r\n", val);
    } else {
        printf("#DBG Clock divider: Reserved value\r\n");
    }

#define ISEN(e)  ((OSCENbits.e)   ? "Enabled," : "        " )
#define ISRDY(r) ((OSCSTATbits.r) ? "Ready"    : "Not ready")

    printf("#DBG EXTOSC:   %s %s\r\n", ISEN(EXTOEN), ISRDY(EXTOR));
    printf("#DBG HFINTOSC: %s %s\r\n", ISEN(HFOEN),  ISRDY(HFOR));
    printf("#DBG MFINTOSC: %s %s\r\n", ISEN(MFOEN),  ISRDY(MFOR));
    printf("#DBG LFINTOSC: %s %s\r\n", ISEN(LFOEN),  ISRDY(LFOR));
    printf("#DBG SOC:      %s %s\r\n", ISEN(SOSCEN), ISRDY(SOR));
    printf("#DBG CRCOSC:   %s %s\r\n", ISEN(ADOEN),  ISRDY(ADOR));

    if (OSCFRQbits.HFFRQ == 0b111) {
        printf("#DBG HFINTOSC Frequency: Reserved\r\n");
    } else {
        printf("#DBG HFINTOSC Frequency: %dMHz\r\n", (1 << OSCFRQbits.HFFRQ));
    }

}
#endif /* CLOCK_DEBUG */

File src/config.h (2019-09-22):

/*
 * Projector Screen Controller
 * 
 * Copyright (c) 2019 Chris Luke. Licensed under SHL-2.0.
 * https://github.com/flirbleoss/projector-screen-controller
 */

#ifndef _CONFIG_H
#define _CONFIG_H

#include <stdint.h>

#define VERSION "0.2"

// Which version of the board to target
#define BOARD_REV_0_1
//#define BOARD_REV_0_2

#ifndef __DEBUG
// Whether we want to use the watchdog timer
#define USE_WATCHDOG
#endif

// Work out and print the current clock situation
//#define CLOCK_DEBUG

// Do we want to enable stdio functions?
#if defined(CLOCK_DEBUG)
#define USE_STDIO
#endif

// Basic test code; not for production use
//#define TEST1   // Alternating LED/Relay pattern
//#define TEST2   // UART1/2 echoback
//#define TEST3   // Timer rollover

#define _XTAL_FREQ      (32000000)  // 32MHz

// Values for Timer1
#define LFINTOSC_FREQ   (31000)
#define SET_TMR1_CS     (0b0100)    // LFINTOSC = 31KHz
#define SET_TMR1_SYNC   (1)         // Use clock directly (no sync)
#define SET_TMR1_PS     (0b00)      // 1:1 prescaler
#define TMR1_COUNT_MAX  (62000)     // Interrupt every 2 seconds
#define TMR1_INTERVAL   (TMR1_COUNT_MAX/LFINTOSC_FREQ)

#define SET_TMR1_RESET_LSB ((uint8_t)((65536-TMR1_COUNT_MAX) & 0xff))
#define SET_TMR1_RESET_MSB ((uint8_t)((65536-TMR1_COUNT_MAX) >> 8))

#define RESET_TMR1() do { \
        TMR1H = SET_TMR1_RESET_MSB; \
        TMR1L = SET_TMR1_RESET_LSB; \
        TMR1IF = 0; \
    } while (0)

#define ENABLE_TMR1() do { \
        TMR1IE = 1; \
        TMR1ON = 1; \
    } while (0)

#define DISABLE_TMR1() do { \
        TMR1ON = 0; \
        TMR1IE = 0; \
        TMR1IF = 0; \
    } while (0)


// Values for Timer0
#define SET_TMR0_CS (0b010)     // Internal clock (Fosc/4)
#define SET_TMR0_PS (0b1111)    // 1:32768 prescaler (~4ms?)

#define RESET_TMR0() do { \
        TMR0H = 0xff; \
        TMR0L = 0xff; \
    } while (0)

#define PAUSE_TMR0() do { \
        TMR0IE = 0; \
        TMR0IF = 0; \
    } while (0)

#define RESUME_TMR0() do { \
        TMR0IE = 1; \
        TMR0IF = 0; \
    } while (0)

#define DISABLE_TMR0() do { \
        T0CON0bits.T0EN = 0; \
        PAUSE_TMR0(); \
    } while (0)

#define ENABLE_TMR0() do { \
        TMR0IE = 1; \
        T0CON0bits.T0EN = 1; \
    } while (0)



// UART settings
#define UART_BRGH 1     // low/high baud rate
#define UART_BRG16 1    // 8/16 bit timer
#define UART_SPBRG 832  // 9600 baud with 32MHz fOSC

// UART handling settings
#define UART_TX_BUF 16  // Send buffer size, per-UART
#define UART_RX_BUF 8   // Receive buffer size, per-UART

// Optional functions
//#define WANT_UART_RECVCOUNT

#endif	/* _CONFIG_H */

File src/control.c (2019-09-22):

/*
 * Projector Screen Controller
 *
 * Copyright (c) 2019 Chris Luke. Licensed under SHL-2.0.
 * https://github.com/flirbleoss/projector-screen-controller
 */

#include "config.h"
#include <xc.h>
#include "pjs.h"
#include <ctype.h>

#define CMD_BUF_SIZ 4

struct ser_control {
    uart_unit_t uart;       // Reference to the associated UART
    char len;               // Number of accumulated characters
    char buf[CMD_BUF_SIZ];  // character buffer
};

typedef enum {
    SER_CTRL_1 = 0,
    SER_CTRL_2,
} ser_ctrl_t;

volatile struct ser_control ser_controls[] = {
    {
        .uart = UART_1,
        .len = 0,
    },
    {
        .uart = UART_2,
        .len = 0,
    }
};

// Control handling

void control_init(void) {
    ser_controls[SER_CTRL_1].len = 0;
    ser_controls[SER_CTRL_2].len = 0;
}

static void command_check_ser(ser_ctrl_t ctrl) {
    volatile struct ser_control *c = &ser_controls[ctrl];
    char uart = c->uart;

    while (!uart_recvempty(uart)) {
        unsigned char ch = uart_recvch(uart, UART_NONBLOCK);

// buggy pre-processor; the isxxxxx macros all fail to generate code, so
// use the function variant
#undef isprint
        if (!isprint(ch)) {
            continue; // skip non-printable chars quickly
        }

        if (!isalnum(ch)) {
            // Command characters always reset the accumulation
            // Any non-alphanumeric is considered a command character
            c->buf[0] = ch;
            c->len = 1;

        } else if (c->len) {
            // Accumulate characters until a valid command is found.
            c->buf[c->len] = ch;
            c->len++;

            // Look for valid commands
            if (c->len == 2) {
                switch (c->buf[1]) {
                case 'P':
                case 'p':
                    // Report current status
                    relay_report(c->uart, c->buf[0]);
                    c->len = 0;
                    break;
                }
            } else if(c->len == 3) {
                relay_channel_t channel;
                relay_direction_t direction;
                char valid = 0;

                switch (c->buf[1]) {
                case '1':
                    channel = RELAY_CH1;
                    ++valid;
                    break;
                case '2':
                    channel = RELAY_CH2;
                    ++valid;
                    break;
                }

                switch (c->buf[2]) {
                case 'S':
                case 's':
                    direction = RELAY_STOP;
                    ++valid;
                    break;
                case 'U':
                case 'u':
                    direction = RELAY_UP;
                    ++valid;
                    break;
                case 'D':
                case 'd':
                    direction = RELAY_DOWN;
                    ++valid;
                    break;
                }

                if (valid == 2) {
                    relay_control(channel, direction);
                    c->len = 0;
                    relay_report(c->uart, c->buf[0]);
                }

            } else {
                // Command too long; reset
                c->len = 0;
            }
        } // else { drop character }
    }
}

void command_check(void) {
    command_check_ser(SER_CTRL_1);
    command_check_ser(SER_CTRL_2);
}

void button_check_channel(relay_channel_t channel, char up, char dn) {
    relay_direction_t direction;

    if (!up && !dn) return; // Test first; most common case
    else if(up && !dn) direction = RELAY_UP;
    else if(!up && dn) direction = RELAY_DOWN;
    else direction = RELAY_STOP;

    relay_control(channel, direction);

    relay_report(UART_1, '#');
    relay_report(UART_2, '#');
}

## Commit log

2019-08-31 Projector Screen Controller
    - Basic schematic and board layout
    [MCU.sch, Power.sch, Relay.sch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]
2019-09-01 Add button 2, LEDs, TVS diode
    * Add button 2; rewire to match the prototype
    * Add a TVS diode across the 12V rail; value TBD
    * Rework power nets into the power sheet; don't use the globals
    inside the sheet, expose the rails as pins.
    * Move power protection inside the power sheet.
    * Add power LEDs
    [MCU.sch, Power.sch, Relay.sch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]
2019-09-01 Update README, add ground planes, adjust clearance
    * Update the README with background and a 3d preview image.
    * Add ground planes to front and back of logic section; add an earth plane on
    back of line voltage section.
    * Check clearances around line voltage input section.
    * Change mounting holes to a standard type with plated flange.
    [projector-screen-controller.kicad_pcb]
2019-09-02 Add Solderpad SHL-2.0 license
    [MCU.sch, Power.sch, Relay.sch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]
2019-09-02 Update fuse footprint, add more 3d models, update TODO
    [Power.sch, projector-screen-controller.kicad_pcb, projector-screen-controller.sch]
2019-09-02 Add relay status LEDs
    [Relay.sch, projector-screen-controller.kicad_pcb]
2019-09-02 Add nominal LED R values; ground plane tweaks; first board spin
    [Power.sch, Relay.sch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]
2019-09-02 Bump revision to 0.2
    [MCU.sch, Power.sch, Relay.sch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]
2019-09-02 Skeleton firmware
    * Basic hardware initialization
    * Template for interrupt handling
    * Details over timers, etc still needs to be worked out
2019-09-02 Basic UART handling
    * Circular buffers for TX and RX, for UART1 and UART2
    * Wiring for TX and RX on UART interrupts
    * Basic primitives for writing to and reading from buffers
    * Not tested yet
2019-09-03 UART size fix
    * Off-by-one in one comparison
    [uart.c]
2019-09-07 Minor layout tweaks, component updates
    * Add an MCU driven status LED
    * Update LED current limit resistor values
    * Minor trace tweaks for clearance
    * Based on empirical measurements of rev 0.1 board, adjust the location of the
    board mounting holes.
    [MCU.sch, Power.sch, Relay.sch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]
2019-09-07 UART fixes; test code
    * UART tweaks;
    * Disable ADCs (pin thieves!)
    * Add missing BRG16 flag
    * Be complete about the PPS setup (though empirically not necessary)
    * Manage interrupts around some critical code
    * Add simple test code to the main loop;
    * Alternating LED/Relay pattern
    * UART echo-back
    * Add a version number string
    * Start some button input de-bounce logic
    * ICD4 project configuration
    * README & .gitignore updates
    [config.h, main.c, uart.c]
2019-09-08 Split the 5v and 12v ground paths
    * To control the return path for (noisy) relay current, split the grounds for
    the 12v and 5v sections.
    * The grounds are joined by bridges (solder pads) placed adjacent to the 5v
    regulator, on both layers.
    * The gound plane is split in two; conveniently the 12v vs 5v components were
    already well placed to make this straightforward.
    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
    [MCU.sch, Power.sch, Relay.sch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]
2019-09-08 Add a smattering of ground vias
    [projector-screen-controller.kicad_pcb]
2019-09-08 First approximation of a working system
    - Working relay control, with timed shutoff
    - Working serial command input with basic feedback
    - Note: No button control yet
    - Now a C99 compliant project (previously was xc8's interpretation of C90)
    - Bugfix in UART FIFO; off-by-one on buffer put rollover
    - Wrapped unused function in ifdef for now to cease a warning
    [config.h, control.c, main.c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]
2019-09-08 Update board symbols, minor ground plane fixes
    * Fuse rating, board maximums
    * ESD logo
    * WEEE logo
    * Some ground plane fixes around the MAX232
    [projector-screen-controller.kicad_pcb]
2019-09-09 First approximation of button handling
    - De-bounce input lines by effectively comparing the input line at both
    time interrupt time and after a short timer expires.
    - Reset the timer if any input line triggers. It's a short period, but
    the assumption is that 'stop' is the combination of the 'up' and
    'down' buttons and there may be a short delay before both lines are
    engaged; so long as it's less than the de-bounce interval then we will
    record both lines once the interval expires.
    - Main loop latches the de-bounced values in a re-entrant friendly way.
    Otherwise we risk subsequent presses overwriting the value as we're
    processing them.
    [control.c, main.c, relay.c]
2019-09-13 Button read fixes
    * Properly initialize timer 0; enable it and TMR0 is not a 16-bit overlay
    of the L and H sections so reset those independently
    * We want the falling edge; sense is not inverted like other platforms
    * Likewise, need to invert the port read, since it's active low; oddity here
    though, bitwise-invert (~) works in the straight assignment case (a = ~b)
    but will not compile in a slightly more involved expression (a = b & ~c) -
    need to work out why
    * Interrupt on change seems to flag 'down' as well as 'up' inputs when 'up' is
    pressed, need to work out if this is a hardware issue
    * Switch compilation mode to hybrid; no need for a call stack all the time
    [config.h, main.c]
2019-09-13 Fix KiCad 4 footprints
    * Update the Phoenix connectors with KiCad 5 footprints
    [projector-screen-controller.kicad_pcb, projector-screen-controller.sch]
2019-09-13 Update all footprints to KiCad 5 paths
    * All footprints updated.
    * 3D models for the relays seem to be missing from KiCad, however, so I
    have a copy in my personal library. Mostly cosmetic.
    [MCU.sch, Power.sch, Relay.sch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]
2019-09-13 Minor cleanup to layout
    [projector-screen-controller.kicad_pcb]
2019-09-13 Channel 2 buttons are reversed; fix in code
    [main.c]
2019-09-13 Serial protocol tweaks
    * Add serial reports, to both UARTs, whenever button presses result in
    action
    * Ignore all non-printable characters received
2019-09-13 Fix channel 2 button reversal
    * The hierarchical schematic pins for channel 2 buttons were reversed in the
    root schematic. Correct this, and add board revision logic to the firmware so
    board versions can be targeted by the build.
    [MCU.sch, Power.sch, Relay.sch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]
2019-09-13 Update gerbers; minor layout tweaks
    * Add ICSP text next to ISCP header
    * Better spacing around channel 2 button traces
    * Update 3d preview, gerbers and board PDF
    [projector-screen-controller-B_Cu.gbr, projector-screen-controller-B_Mask.gbr, projector-screen-controller-B_SilkS.gbr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]
2019-09-14 Add a simple clock diagnostic
    * Dump various system clock statuses
    * Adds a way to use stdlib stdio on UART 1
2019-09-14 Relay reporting after button presses and timer expiration
    * Use a flag to signal relay reporting to the UARTS
    * Report after button presses have been executed
    * Report when relays turn off at timer expiration
2019-09-14 Workaround for potential compiler bug
    * The ctypes macros for detecting ASCII character class seem to confuse the
    compiler into not generating code for them. By undefining the 'isprint'
    macro we fall-through to the stdlib implementation instead.
    [control.c]
2019-09-14 Timer cleanup
    * Rework some of the timer management. This started as an exercise in reducing
    compiler warnings at the highest setting (though that proved fruitless when it
    came to type size reduction to __bit values). Instead ended up breaking out some
    of the timer management macros for better control of what is going on. Still a
    slight inconsistency between Timer0 and Timer1, but nothing egregious.
    [config.h, main.c, uart.c]
2019-09-18 Adjust ground plane clearance, LED margin clearances
    * For PCB DRC checks, fix clearances.
    * Make AC section tracks slightly larger.
    [MCU.sch, Power.sch, Relay.sch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]
2019-09-18 Add/correct a bunch of part numbers
    [MCU.sch, Power.sch, Relay.sch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]
2019-09-21 Layout adjustments to make room
    * Move the relays and diodes left to give a little more room to the
    power connectors; adjust ground planes to suit, etc.
    * Larger footprint for TVS diode; related adjustments.
    * Other minor adjustments to layout.
    * Add board-only preview.
    [MCU.sch, Power.sch, Relay.sch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]
2019-09-21 Update gerbers and PDFs
    [projector-screen-controller-B_Cu.gbr, projector-screen-controller-B_Mask.gbr, projector-screen-controller-B_SilkS.gbr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]
2019-09-22 Via tweaks; update earth flood
    * Tweak some via locations.
    * Update some of the earth flood fill around relay pins that was missed
    previously.
    [projector-screen-controller.kicad_pcb]
2019-09-22 Fix receiving on UART 2
    * Typo in the control polling loop; was checing UART_1 twice and UART_2
    not at all.
    * Use enum types for UART channels and control serial units, to
    improve type checking.
    * Bump to firmware version 0.2.
    [config.h, control.c, uart.c]
2019-09-23 Update xtal load capacitors, fix left mounting holes
    * Try some 33pF caps for the crystal.
    * Reflect the left side mounting holes in the schematic.
    * Reroute one RS232 TTL line; though now more stuff runs under the clock
    lines so may move all the RS232 TTL traces later.
    [MCU.sch, Power.sch, Relay.sch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]
2019-09-28 Make room for input filtering
    * Move the crystal block up and isolate its ground plane.
    * Route the RS232 TTL signals around the crystal block.
    * Update images, PDFs and gerbers.
    [MCU.sch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]
2019-09-28 First pass at input protection for buttons
    * Schottky diodes & capacitors to limit and smooth the inputs.
    * Relies on the WPU of the MCU to provide a charge for the C (possibly
    a bad idea, will see).
    * Had to move a bunch of stuff to make room and make sure the ground paths
    were sensible.
    * Update all the disc capacitors to the Kicad 5 footprint.
    [MCU.sch, Power.sch, Relay.sch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]

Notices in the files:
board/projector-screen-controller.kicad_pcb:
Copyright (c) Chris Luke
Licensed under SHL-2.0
